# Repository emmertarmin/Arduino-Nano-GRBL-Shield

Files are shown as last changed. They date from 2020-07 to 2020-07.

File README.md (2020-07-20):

# Arduino-Nano-GRBL-Shield
This CNC Shield was designed to replace a "Stepper Bricklet" from Tinkerforge. It is much larger in size, but the four screw holes are compatible in size and placement.

## Features
- 102mm x 50mm
- Arduino Nano pinout is designed for GRBL firmware.
- 3 individual "X-Y-Z" stepper drivers, with a fourth "A" Axis whose `step` and `dir` pins can be coupled with either of the other three axes.
- Limit switches per axis are connected in series for NC switch operation. This means the Arduino is going to expect a closed circuit on all 6 switches (if switches are enabled in the firmware) and interpret an open circuit as a triggered switch.
- Switches have RC circuits as is [recommended by GRBL](https://github.com/gnea/grbl/wiki/Wiring-Limit-Switches) for noise filtering. These SMD parts can be left unpopulated.
- 12V Barrel Jack power source for stepper motors.
- If Arduino is to be driven without an active USB connection, the 12V source is to be stepped down to 6-7 Volts with a switching regulator. I used [this DSN-1504 one](https://www.hestore.hu/prod_10038118.html?lang=en) from Hestore.
- The only smd parts that are needed for operation are one 10k pullup resistor on the `EN` pin under the Arduino, and 12 pieces of 100k pulldown resistors right next to the stepper drivers, which control `MS1-MS3` pins to set microstepping.

> Please make sure your Arduino Nano can handle an external 6-7V source on VIN and an active USB connection simultaneously. Officially it should be able to do that, but there's stories on the internet about versions of Nanos that got burnt.

> Also, while a direct 12V source on the VIN of the Arduino is officially fine, it's not recommended, as the internal regulator of the Arduino will dissipate the 7V difference in form of heat. This is why I used a switching step-down converter.

## Images

Renders were created with [tracespace.io](https://tracespace.io/)

Top

Bottom

The images below show an earlier version which lacked the RC filters. Apart from that it's the same. Please excuse the dusty Nano.

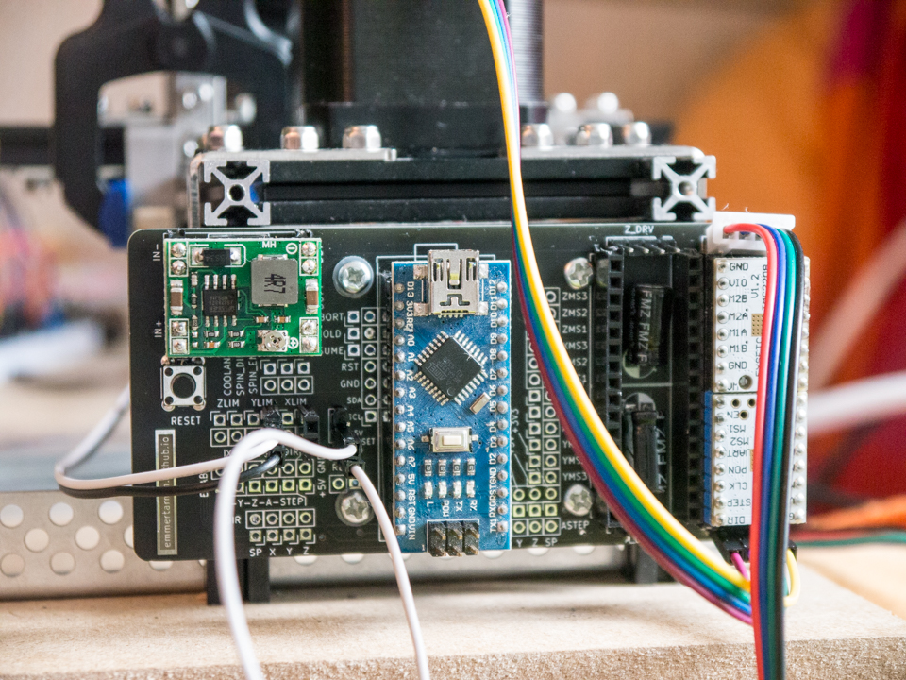
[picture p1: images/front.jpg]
Front


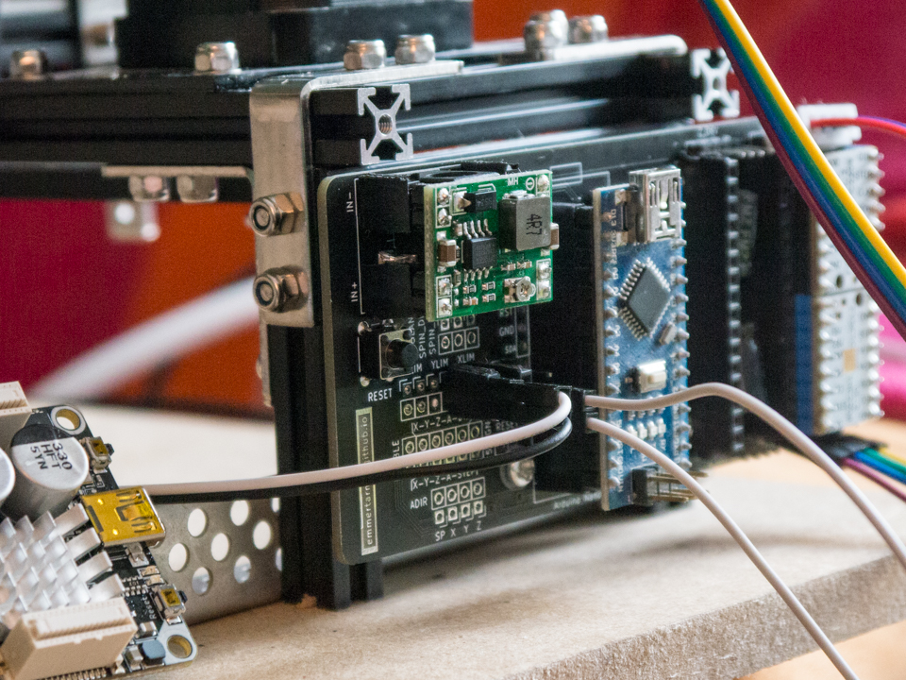
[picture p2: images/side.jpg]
Side


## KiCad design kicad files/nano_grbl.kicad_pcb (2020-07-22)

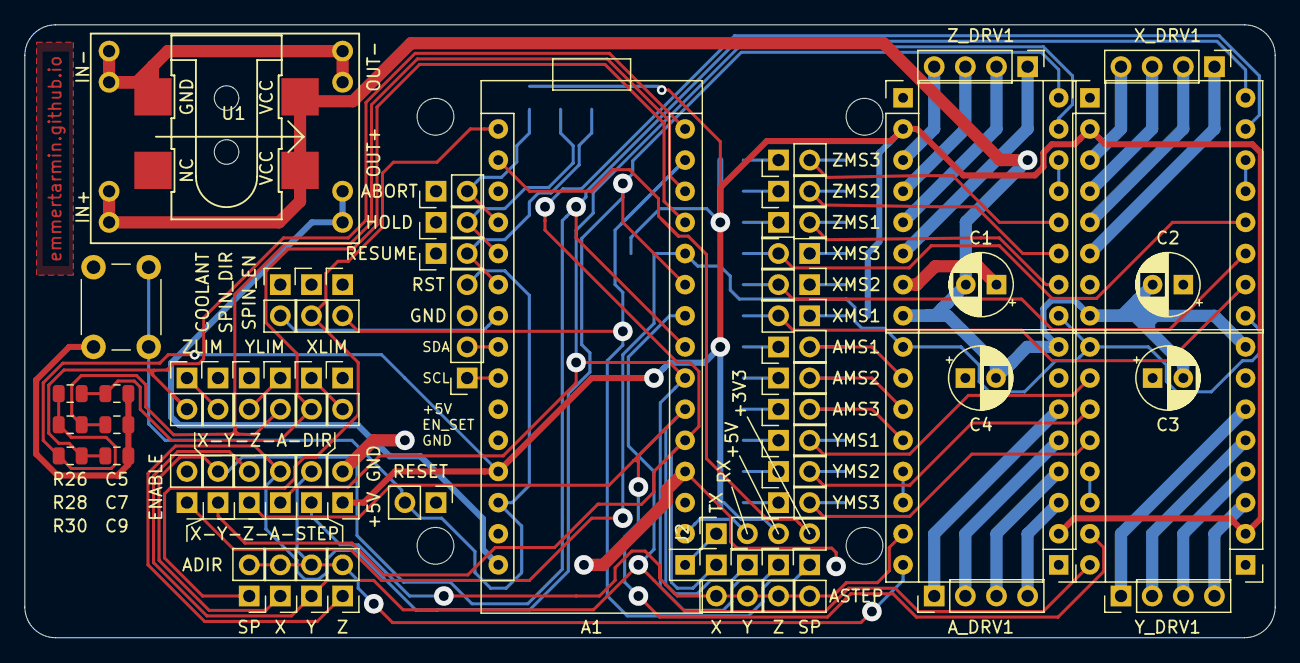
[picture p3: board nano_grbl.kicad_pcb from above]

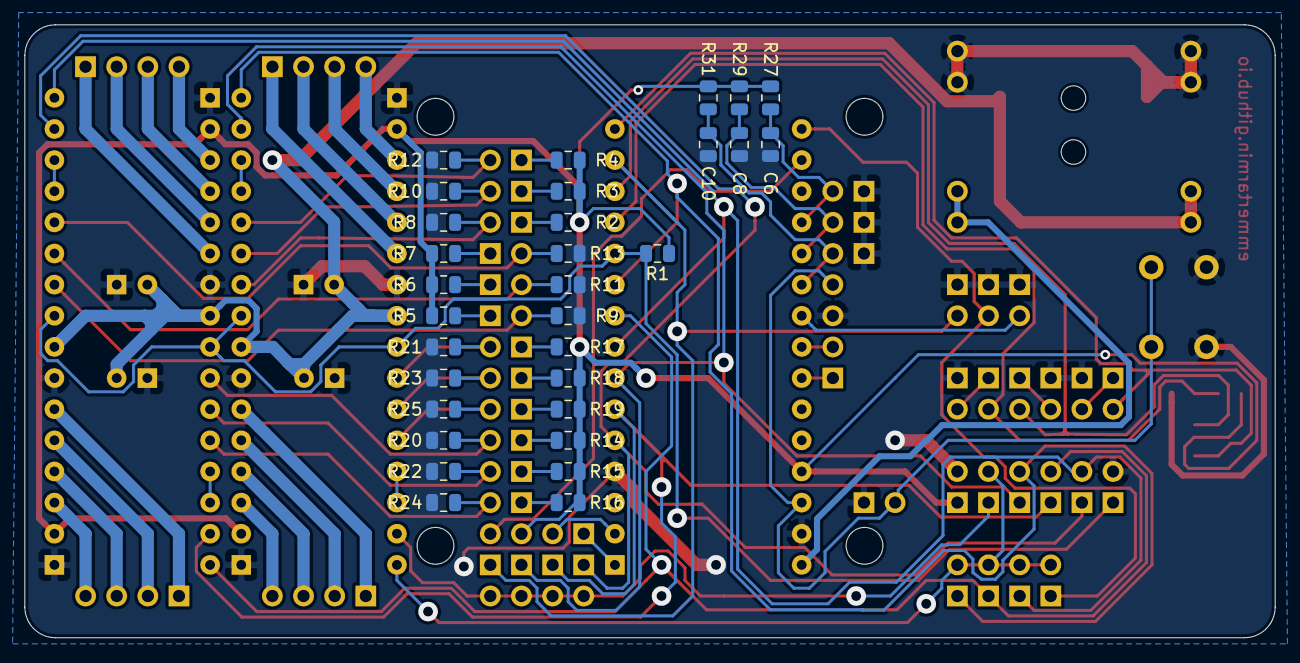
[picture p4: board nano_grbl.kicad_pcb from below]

Board: 2 copper layers, 102.0 x 50.0 mm, 94 parts (31 on the bottom side), 75 nets.

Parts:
A1: Arduino_Nano_v3.x; Arduino_Nano
A_DRV1: A_DRV; Pololu_Breakout-16_15.2x20.3mm
C1, C2, C3, C4: 100uF; CP_Radial_D5.0mm_P2.50mm
C5, C6, C7, C8, C9, C10: 100nF; C_0805_2012Metric
J1: Barrel_Jack; Barrel_Jack_2.1x5.5_Custom_SMT
J2: UART; PinSocket_1x04_P2.54mm_Vertical
J3: I2C; PinSocket_1x04_P2.54mm_Vertical
J5: ZMOT; PinHeader_1x04_P2.54mm_Vertical
J6: XMOT; PinHeader_1x04_P2.54mm_Vertical
J7: YMOT; PinHeader_1x04_P2.54mm_Vertical
J8: AMOT; PinHeader_1x04_P2.54mm_Vertical
JP1: ESTOP; PinHeader_1x02_P2.54mm_Vertical
JP2, JP3, JP4, JP5, JP6, JP7, JP8, JP9, JP10, JP11, JP12, JP13, JP14, JP15, JP16, JP17, JP18, JP19, JP20, JP21, JP22, JP23, JP24, JP25, JP26, JP27, JP28, JP29, JP30, JP31, JP32, JP33, JP34, JP35, JP36, JP37, JP38, JP39: Jumper_NO_Small; PinHeader_1x02_P2.54mm_Vertical
R1, R2, R3, R4, R5, R6, R7, R14, R15, R16, R17, R18, R19, R26, R27, R28, R29, R30, R31: 10K; R_0805_2012Metric
R8, R9, R10, R11, R12, R13, R20, R21, R22, R23, R24, R25: 100K; R_0805_2012Metric
SW1: SW_Push; SW_PUSH_6mm
U1: buck_conv
X_DRV1: X_DRV; Pololu_Breakout-16_15.2x20.3mm
Y_DRV1: Y_DRV; Pololu_Breakout-16_15.2x20.3mm
Z_DRV1: Z_DRV; Pololu_Breakout-16_15.2x20.3mm

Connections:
+3V3: A1.17, J2.4
+5V: A1.27, A_DRV1.2, J2.3, JP11.1, R1.1, R2.2, R3.2, R4.2, R5.2, R6.2, R7.2, R14.2, R15.2, R16.2, R17.2, R18.2, R19.2, R26.1, R27.1, R28.1, R29.1, R30.1, R31.1, X_DRV1.2, Y_DRV1.2, Z_DRV1.2
+12V: A_DRV1.8, C1.2, C2.2, C3.2, C4.2, J1.1, U1.1, X_DRV1.8, Y_DRV1.8, Z_DRV1.8
ABORT: A1.19, C6.2, JP25.2, R27.2
ADIR: A_DRV1.16, JP10.2, JP12.2, JP13.2, JP14.2, JP15.2
ASTEP: A_DRV1.15, JP2.2, JP3.2, JP4.2, JP5.2, JP10.1
COOLANT: A1.22, JP24.2
EN: A1.11, A_DRV1.9, JP6.1, R1.2, X_DRV1.9, Y_DRV1.9, Z_DRV1.9
GND: A1.4, A1.29, A_DRV1.1, A_DRV1.7, C1.1, C2.1, C3.1, C4.1, C5.1, C6.1, C7.1, C8.1, C9.1, C10.1, J1.2, J3.3, JP1.1, JP6.2, JP11.2, JP17.1, JP19.1, JP21.1, JP22.1, JP23.1, JP24.1, JP25.1, JP26.1, JP27.1, R8.2, R9.2, R10.2, R11.2, R12.2, R13.2, R20.2, R21.2, R22.2, R23.2, R24.2, R25.2, SW1.1, U1.2, U1.4, X_DRV1.1, X_DRV1.7, Y_DRV1.1, Y_DRV1.7, Z_DRV1.1, Z_DRV1.7
HOLD: A1.20, C8.2, JP26.2, R29.2
unnamed: A1.30, U1.3
unnamed: A_DRV1.3, J8.4
unnamed: A_DRV1.4, J8.3
unnamed: A_DRV1.5, J8.2
unnamed: A_DRV1.6, J8.1
unnamed: A_DRV1.10, JP37.2, R21.1
unnamed: A_DRV1.11, JP38.2, R23.1
unnamed: A_DRV1.12, JP39.2, R25.1
unnamed: A_DRV1.13, A_DRV1.14
unnamed: J5.1, Z_DRV1.6
unnamed: J5.2, Z_DRV1.5
unnamed: J5.3, Z_DRV1.4
unnamed: J5.4, Z_DRV1.3
unnamed: J6.1, X_DRV1.6
unnamed: J6.2, X_DRV1.5
unnamed: J6.3, X_DRV1.4
unnamed: J6.4, X_DRV1.3
unnamed: J7.1, Y_DRV1.6
unnamed: J7.2, Y_DRV1.5
unnamed: J7.3, Y_DRV1.4
unnamed: J7.4, Y_DRV1.3
unnamed: JP16.1, JP17.2
unnamed: JP18.1, JP19.2
unnamed: JP20.1, JP21.2
unnamed: JP28.1, R2.1
unnamed: JP28.2, R8.1, Z_DRV1.10
unnamed: JP29.1, R3.1
unnamed: JP29.2, R10.1, Z_DRV1.11
unnamed: JP30.1, R4.1
unnamed: JP30.2, R12.1, Z_DRV1.12
unnamed: JP31.1, R5.1
unnamed: JP31.2, R9.1, X_DRV1.10
unnamed: JP32.1, R6.1
unnamed: JP32.2, R11.1, X_DRV1.11
unnamed: JP33.1, R7.1
unnamed: JP33.2, R13.1, X_DRV1.12
unnamed: JP34.1, R14.1
unnamed: JP34.2, R20.1, Y_DRV1.10
unnamed: JP35.1, R15.1
unnamed: JP35.2, R22.1, Y_DRV1.11
unnamed: JP36.1, R16.1
unnamed: JP36.2, R24.1, Y_DRV1.12
unnamed: JP37.1, R17.1
unnamed: JP38.1, R18.1
unnamed: JP39.1, R19.1
unnamed: X_DRV1.13, X_DRV1.14
unnamed: Y_DRV1.13, Y_DRV1.14
unnamed: Z_DRV1.13, Z_DRV1.14
RESET: A1.3, A1.28, J3.4, JP1.2, SW1.2
RESUME: A1.21, C10.2, JP27.2, R31.2
RX: A1.2, J2.2
SCL: A1.24, J3.1
SDA: A1.23, J3.2
SPIN_DIR: A1.16, JP15.1, JP23.2
SPIN_EN: A1.14, JP5.1, JP22.2
TX: A1.1, J2.1
XDIR: A1.8, JP7.2, JP12.1, X_DRV1.16
XLIMIT: A1.12, C5.2, JP20.2, R26.2
XSTEP: A1.5, JP2.1, JP7.1, X_DRV1.15
YDIR: A1.9, JP8.2, JP13.1, Y_DRV1.16
YLIMIT: A1.13, C7.2, JP18.2, R28.2
YSTEP: A1.6, JP3.1, JP8.1, Y_DRV1.15
ZDIR: A1.10, JP9.2, JP14.1, Z_DRV1.16
ZLIMIT: A1.15, C9.2, JP16.2, R30.2
ZSTEP: A1.7, JP4.1, JP9.1, Z_DRV1.15

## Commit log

2020-07-20 extended README
    [nano_grbl.kicad_pcb, nano_grbl.sch]
2020-07-22 corrected RxTx silkscreen
    [nano_grbl.kicad_pcb]
